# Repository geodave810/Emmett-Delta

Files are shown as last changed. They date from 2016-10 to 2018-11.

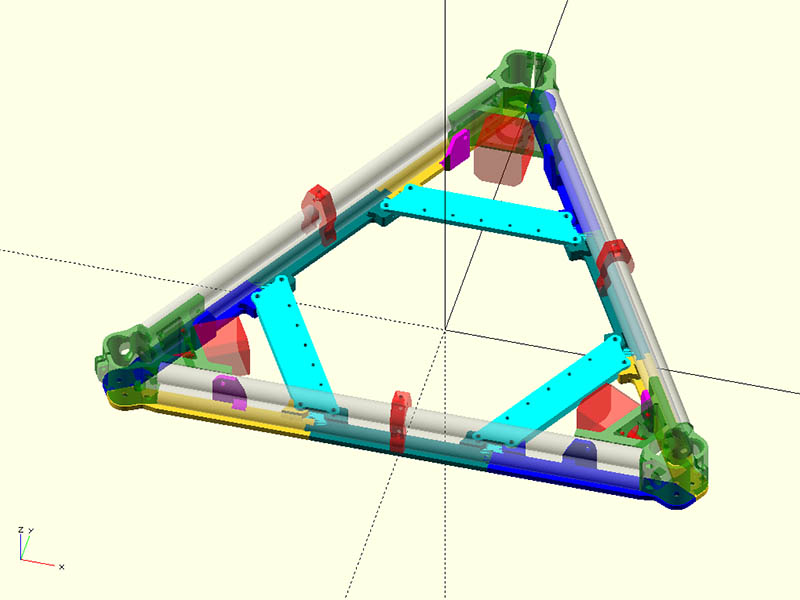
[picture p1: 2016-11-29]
EMT12_Horizontal_EMT12_Vertical/BottomFrame/BottomDoveTailFrame_300mmOD_Rev30.jpg

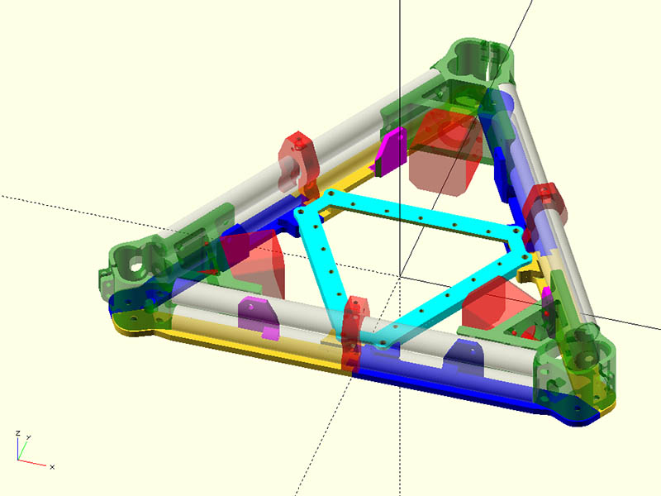
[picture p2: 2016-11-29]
EMT12_Horizontal_EMT12_Vertical/BottomFrame/BottomDoveTailFrame_210mmOD_Rev30.jpg

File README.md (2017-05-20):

# Emmett-Delta
Delta 3d Printer using Electrical Metal Tubing (EMT)

For details about this Delta 3d printer see the build log & discussion here:
<a href="http://www.openbuilds.com/builds/emmett-delta.3052/">Emmett-Delta</a>

I have added an animation file that shows how all the parts go together for Option 3 build
The animation was created using <a href="https://github.com/PRouzeau/OpenSCAD-Delta-Simulator">PRouzeau OpenSCA-Delta-Simulator</a>

10/31/2016 Update:
There are several different build options for this Delta & I am just getting
all these files together on Github.  Each Option will have its own file folder.
There is a BOM spreadsheet file, but it needs to be updated some.

Option 1:
3/4" EMT Horizontals and V-Slot 2060 extrusions for the Verticals.
(This is what I originally set out to build, but changed to the Option 3 build)

Option 2:
3/4" EMT Horizontals & 4x 1/2" EMT Verticals on each column.
You can also find his Cobalt Griffonary's nice build log of this configuration here:

https://cobaltgriffonary.blogspot.ca/2016/10/project-proteus-delta-part-1.html
https://cobaltgriffonary.blogspot.ca/2016/10/project-proteus-delta-part-2.html
https://cobaltgriffonary.blogspot.ca/2016/11/project-proteus-delta-part-3.html
https://cobaltgriffonary.blogspot.ca/2016/11/project-proteus-delta-part-4.html
https://cobaltgriffonary.blogspot.ca/2016/11/project-proteus-delta-part-5.html
https://cobaltgriffonary.blogspot.ca/2016/12/project-proteus-delta-part-6.html
https://cobaltgriffonary.blogspot.ca/2017/01/project-proteus-delta-part-7.html
https://cobaltgriffonary.blogspot.ca/2017/05/project-proteus-delta-part-8.html

Option 3:
1/2" EMT Horizontals & 4x 1/2" EMT Verticals on each column.
(This is the build I am doing & this has the most current changes)

Option 4:
1/2" PVC Horizontals & 4x 1/2" EMT Verticals on each column.

Option 5:
1/2" PVC Horizontals & 4x 1/2" PVC Verticals on each column.
(I have not uploaded the vertex files for this yet)

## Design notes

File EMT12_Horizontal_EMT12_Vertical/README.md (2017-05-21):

Update Info 5/21/2017

The build I am planning should have a build diameter of 200mm x 590mm height.  I am currently redoing the vertex parts for this version & printing them this week.

EMT Cut Lengths:
12x 700mm Lengths for Vertical 1/2" EMT
12x 266.5mm Lengths for Horizontal 1/2" EMT

This folder consists of the files specific to the 1/2"EMT Horizontal & 1/2" EMT Vertical Build.
The Filament Holder, HeatBed Brackets, P/S Brackets & various jigs can be found in folders under the main folder.

The reason they are not in this folder is because the openscad used to generate the STL files
has options for the various builds.

https://github.com/geodave810/Emmett-Delta/tree/master/FilamentHolder

https://github.com/geodave810/Emmett-Delta/tree/master/HB_Brackets

https://github.com/geodave810/Emmett-Delta/tree/master/PS_Brackets

https://github.com/geodave810/Emmett-Delta/tree/master/Jigs

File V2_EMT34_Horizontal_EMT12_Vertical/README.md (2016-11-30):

In an effort to make the vertex parts more consistant between the different configurations,
I am modifying the 3/4" EMT Horizontals.  This will use a quite a bit less plastic as well.
The Vertex_2x_EMT34H_4xEMT12V_V2_rev101.stl file can be used for bottom or top but has no belt adjustment
TheVertexTop_2x_EM34TH_4xEMT12V_V2_rev101.stl has Belt adjustment & also uses 2 pipes on each side.

The Heat Bed Brackets can be found in the folder:

https://github.com/geodave810/Emmett-Delta/tree/master/HB_Brackets

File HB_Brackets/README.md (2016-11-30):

These are the Heat Bed Brackets for the different options of Emmett-Delta Build.
There are 3 different STL files as well as an openscad file that uses the .dxf file for the profiles.

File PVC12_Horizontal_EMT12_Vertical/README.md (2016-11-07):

These are the files you need if configuring this build for 1/2" PVC for the Horizontals & 1/2" EMT for the Verticals.

The big advantage to this configuration is drill the mounting holes should be easier with PVC than with EMT.

For a 300mm Build plate, the horizontal PVC would only be 16.4" long & only 6.4" between Vertex screw hole &
where the build plate connects to Heat Bed Bracket.

See the HB_Bracket & PS_Brackets folder fot the bracket to hold the Heat Bed & Power Supply
https://github.com/geodave810/Emmett-Delta/tree/master/HB_Brackets

https://github.com/geodave810/Emmett-Delta/tree/master/PS_Brackets

See the following folder for parts that mount to the Vertical 1/2" EMT & Idler bracket

https://github.com/geodave810/Emmett-Delta/tree/master/EMT12_Horizontal_EMT12_Vertical

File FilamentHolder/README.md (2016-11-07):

This is what I am using for the Filament holder with this build.

The original design for this filament holder is here: http://www.thingiverse.com/thing:508896

Here are the references to the modifications I did to this design which include openscad sources.

Customizable Spool Holder Base
http://www.thingiverse.com/thing:1751711

Parametric openscad Remix of Universal stand-alone filament spool holder
http://www.thingiverse.com/thing:1715713

Remix of Filament Guide Tube to convert to openscad and make Parametric
http://www.thingiverse.com/thing:1710043

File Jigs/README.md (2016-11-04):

This folder is for assorted Jigs I am using with building this design.

The Horizontal Pipe Drill Jigs are to help drill straight holes thru center of the Pipes.
I would still recommend using a drill press to drill the holes.
There is a drill jig for 1/2" EMT, 3/4" EMT & 1/2" PVC pipe.

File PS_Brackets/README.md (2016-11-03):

These are brackets that allow you to mount a Power Supply to one side of the Delta on the bottom 2 pipes.
For the Extended Brackets, you will need to mirror 1 of them for the other side.  The extended brackets
should work better for smaller Build Diameter like 200mm.  See the animation file for how these look assembled.

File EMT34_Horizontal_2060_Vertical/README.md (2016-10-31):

These are the files for building a Emmett-Delta using 3/4" EMT for the Horizontals & V-Slot 2060 for the Verticals.

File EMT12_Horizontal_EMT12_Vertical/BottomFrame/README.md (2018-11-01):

This is a frame assembly that helps to pull all the parts together.
With this method, the horizontal 1/2" EMT should be able to stay in place
by connecting the vertex parts to this & using the vertex brackets.
This will save you from having to drill holes thru the horizontal 1/2" EMT.

The openscad source file references Vertex_2x_EM12TH_4xEMT12V_rev100.stl

Before printing any of these parts, I would recommend printing the file:
BottomDoveTailFrame_Test_Rev30.stl first.
This should give you a good indication of the fit of the dovetails & screw holes.

The holes are sized for M4 or #8 screws on the dovetail vertex mounting holes
The locknut traps are sized for #8 locknuts.  Change the variable:
M4Nut_OD = 9.4;   //If you want to use M4 screws & locknuts
The holes for mounting electronics brackets or electronics on the inside frame
are sized for M3 Screws.

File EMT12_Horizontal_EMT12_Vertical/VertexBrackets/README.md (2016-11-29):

This folder contains the brackets used to hole the 1/2" EMT horzontal pipe to the Vertex and/or Dovetail Inner Frame.

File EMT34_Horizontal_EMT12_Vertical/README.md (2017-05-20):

These are the Vertex and additionals Parts you need if you are building the Emmett-Delta with 3/4" EMT Horizontals & 1/2" EMT Verticals.

You can also find his Cobalt Griffonary's nice build log of this configuration here:
https://cobaltgriffonary.blogspot.ca/2016/10/project-proteus-delta-part-1.html
https://cobaltgriffonary.blogspot.ca/2016/10/project-proteus-delta-part-2.html
https://cobaltgriffonary.blogspot.ca/2016/11/project-proteus-delta-part-3.html
https://cobaltgriffonary.blogspot.ca/2016/11/project-proteus-delta-part-4.html
https://cobaltgriffonary.blogspot.ca/2016/11/project-proteus-delta-part-5.html
https://cobaltgriffonary.blogspot.ca/2016/12/project-proteus-delta-part-6.html
https://cobaltgriffonary.blogspot.ca/2017/01/project-proteus-delta-part-7.html
https://cobaltgriffonary.blogspot.ca/2017/05/project-proteus-delta-part-8.html

I have also included Cobalt Griffonary's basic BOM list in this for this configuration in this folder

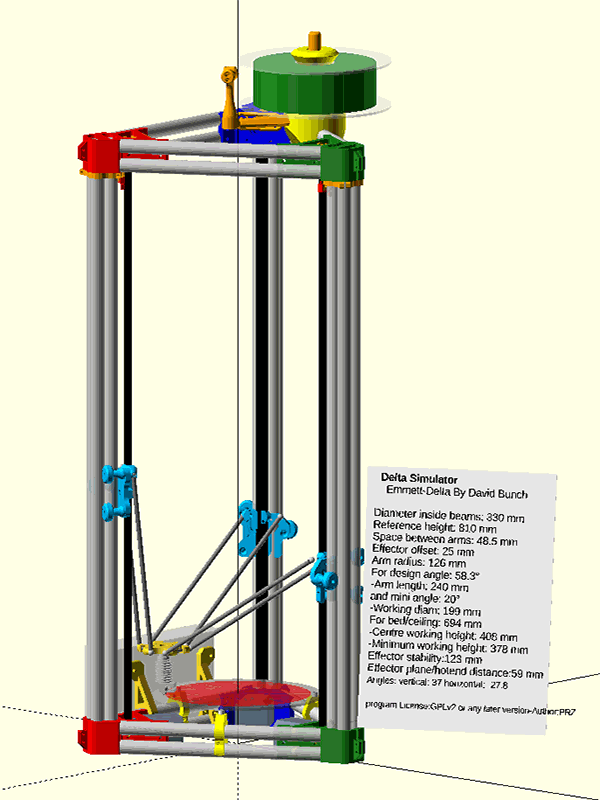
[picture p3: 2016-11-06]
Animations/Emmett_Animation_EMT12x266mmH_EMT12x800mmV.gif

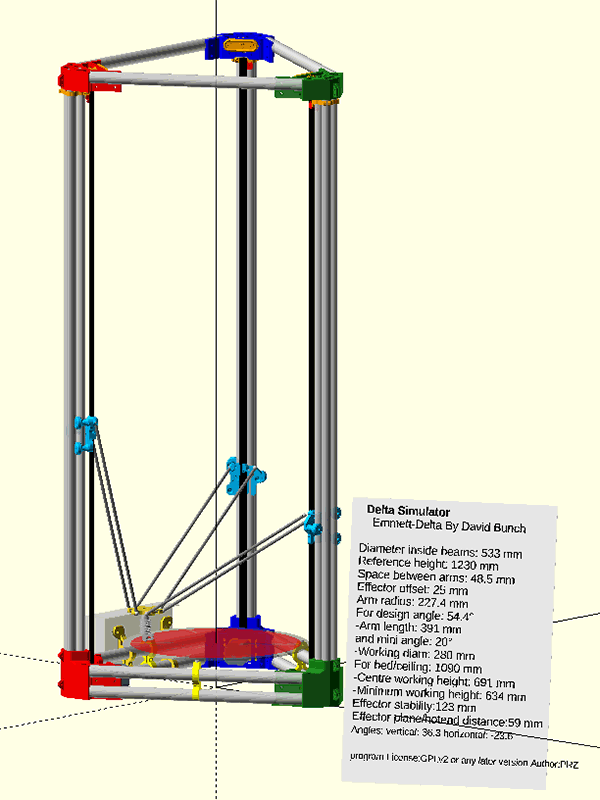
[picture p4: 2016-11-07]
Animations/Emmett_Delta_EMT34x420mmH_EMT12x1220mmV.gif

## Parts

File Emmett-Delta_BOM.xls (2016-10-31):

2016-01-08 | Bill of Materials for Emmett Delta Printer
Quantity | Description | Cost | Total Cost |  | Totals | Purchase Link
 | Plastic Filament |  |  |  |  | I am using Blue & Yellow PETG for the colors of plastic parts
3 | eSUN PETG Filament 1kg 1.75mm Plastic (My Hotend is 1.75mm) | $24.95 | $74.85 | $74.85 |  | http://www.intservo.com/products/esun-petg-filament-1-75mm-1kg-spool?variant=963058195
3 | eSUN PLA Filament 1kg 1.75mm Plastic (Option) | $21.99 | $65.97 |  | $74.85 | http://www.intservo.com/products/pla-filament-175?variant=800124003
 | Openbuilds Parts |  |  |  |  | I am using 1.75mm PETG filament, but you might need 3.00mm & prefer another type of Plastic
3 | 2060 Vertical Aluminum Extrusions (1000mm) | $15.50 | $46.50 |  |  | http://openbuildspartstore.com/v-slot-linear-rail/
 |  |  |  |  |  | My Delta is using 1000mm length, but you could probably go with 1500mm length
12 | Solid V Wheel Kit | $4.85 | $58.20 |  |  | http://openbuildspartstore.com/solid-v-wheel-kit/
 |  |  |  |  |  | You could also use The Delrin V Wheel or the Xtreme Solid V Wheels
6 | Eccentric Spacers 6mm for full size wheels | $2.00 | $12.00 |  |  | http://openbuildspartstore.com/eccentric-spacer/
2 | T-Nuts 1 pack of 25 | $4.95 | $9.90 |  |  | http://openbuildspartstore.com/tee-nuts-25-pack/
 |  |  |  |  |  | 12 T-Nuts for bottom Vertex, 6 or 12 T-Nuts on Top, 3 or 6 T-Nuts for Top Limit Switch Holder
3 | Smooth Idler Pulley Wheel Kit (For Idler pulley at top) | $5.45 | $16.35 |  |  | http://openbuildspartstore.com/smooth-idler-pulley-wheel-kit/
12 | M5 x 45mm for putting plates on both sides of wheels (Steel Option) | $0.20 |  |  |  | http://openbuildspartstore.com/low-profile-screws-m5/
3 | M5 x 40mm for idler pulley (Steel Option) | $0.20 |  |  |  | http://openbuildspartstore.com/low-profile-screws-m5/
12 | 6mm spacers for wheels on both sides | $0.20 | $2.40 |  |  | http://openbuildspartstore.com/aluminum-spacers/
9 | Precision Shim - 10x5x1mm (Think you can get about the same thing from MrMetric | $0.25 |  |  |  | http://openbuildspartstore.com/precision-shim-10x5x1mm/
 | Shipping $10 to $20 depending on where you are |  | $10.00 | $155.35 | $230.20
 | Local Electrical Conduit Purchase from Home Depot or Lowes (Check OD to be 23.5mm or .925")
2 | 2 - 3/4" x 10' EMT (Electrical Conduit from Home Depot or Lowes) | $3.63 | $7.26 | $7.26 | $237.46
1 | Pipe Cutter if you do not have one (This is one I like, but you can get a less expensive one) | $21.29 |  |  |  | http://www.homedepot.com/p/RIDGID-101-Tubing-Cutter-40617/100075014
 | MrMetric Parts
 | I am generally using 1 locknut per bolt, but added flatwashers to the list just in case
12 | M5x45 Stainless Button Head for Carriage Wheels (Option if you prefer Stainless like I do) | $0.18 | $2.16 |  |  | http://www.mrmetric.com/metric-fasteners/metric-button-socket-screw-ssa2/M11598.html
3 | M5x40 Stainless Button Head for idler Pulley (Option if you prefer Stainless like I do) | $0.23 | $0.69 |  |  | http://www.mrmetric.com/metric-fasteners/metric-button-socket-screw-ssa2/M11486.html
24 | M5X10 Button Head Socket Cap Screw (Only need 24 really for T-slot connect) | $0.10 | $2.40 |  |  | http://www.mrmetric.com/metric-fasteners/metric-button-socket-screw-ssa2/M11521.html
20 | M5x20 Button Head for Motor Mount Plate & Idler plate(18 needed) | $0.17 | $3.40 |  |  | http://www.mrmetric.com/metric-fasteners/metric-button-socket-screw-ssa2/M11526.html
9 | M5x16 Button Head (If Mounting Tetrahedron corners to top Vertex, 9 Tnuts needed also) | $0.13 | $1.17 |  |  | http://www.mrmetric.com/metric-fasteners/metric-button-socket-screw-ssa2/M11524.html
 | You could use Socket Cap instead, but only .01 cheaper & stick out further
100 | M5x.8 Nylon Insert Locknut Stainless Steel A2 (Price Break at 100) | $0.04 | $4.00 |  |  | http://www.mrmetric.com/metric-fasteners/ssa2-metric-nylock-nuts/M50352.html
100 | M5 Stainless Flat Washers (9.6 to 10mmOD, 5.3 to 5.48mmID) | $0.02 | $2.00 |  |  | http://www.mrmetric.com/Discount-Items/Metric-Washers/M60710.html
24 | M4x25mm Socket Cap Screw to attach Brackets around Pipe & vertex | $0.13 | $3.12 |  |  | http://www.mrmetric.com/metric-fasteners/metric-socket-head-cap-screws-ssa2/M10622.html
 | If you using extended brackets, you will need 1 more bolt & locknut per bracket
24 | M4x25mm Button Heads (These look better than Socket head, but a little bit more money $5.52 instead $3.12) | $0.23 | $5.52 |  |  | http://www.mrmetric.com/metric-fasteners/metric-button-socket-screw-ssa2/M11517.html
12 | M4x16mm Button Heads (2 on each vertex for Extended Bracket) | $0.08 | $0.96 |  |  | http://www.mrmetric.com/metric-fasteners/metric-button-socket-screw-ssa2/M11514.html
36 | M4x35mm Socket Head Stainless (If Drilling pipe instead of using brackets $3.60) | $0.15 |  |  |  | http://www.mrmetric.com/metric-fasteners/metric-socket-head-cap-screws-ssa2/M10727.html
 | or you can use 8-32x1 1/2" Phillips head screws & locknuts from local hardware instead of M4x35mm bolts
 | Button heads would look better, but cannot get this length in Button head
100 | M4 Locknuts (Get 100 to make sure you have enough) | $0.02 | $2.00 |  |  | http://www.mrmetric.com/metric-fasteners/ssa2-metric-nylock-nuts/M50351.html
12 | M3x10mm Socket Cap Screws (12 for mounting Motors to Motor Mount) | $0.05 | $0.60 |  |  | http://www.mrmetric.com/metric-fasteners/metric-socket-head-cap-screws-ssa2/M10605.html
3 | M3x16mm Socket Cap Screws (to tighten EMT Clamp that HeatBed attaches to, 14mm length will also work) | $0.06 | $0.18 |  |  | http://www.mrmetric.com/metric-fasteners/metric-socket-head-cap-screws-ssa2/M10608.html
6 | M3x20mm Socket Cap Screws (To tighten parts on EMT on Tetrahedron top if you are using this option) | $0.06 | $0.36 |  |  | http://www.mrmetric.com/metric-fasteners/metric-socket-head-cap-screws-ssa2/M10611.html
100 | M3 Locknuts | $0.03 | $3.00 |  |  | http://www.mrmetric.com/metric-fasteners/ssa2-metric-nylock-nuts/M50350.html
 | M3 Jam Nuts (In case you need these $0.03 if you order 100) | $0.05 |  |  |  | http://www.mrmetric.com/metric-fasteners/ssa2-metric-jam-nut-m3/
 | 14mm length will probably also work, but 16mm is more of standard size
 | I also need bolts to connect Traxxas Rods, but not sure what Length or Size yet
 | Shipping $6 & free shipping of $50 |  | $6.00 | $37.56 | $275.02
 | TriDPrinting Parts
3 | Nema 17 Stepper Motor (76oz-in torque) | $16.65 | $49.95 |  |  | http://www.tridprinting.com/Electronics/
8 | GT2 Belt (I probably only need 7 Meters, but want to make sure I have enough) | $2.50 | $20.00 |  |  | http://www.tridprinting.com/Mechanical-Parts/
1 | GT2 Belt Drive Gear 16 Tooth 16T, 2mm Pitch, 5mm bore (Per 3) | $6.95 | $6.95
1 | 400mm Assembled Traxxas Rods (Set of 6) | $44.95 | $0.00
 | You could save money by buying Unassembled version for $25.95 | $25.95 | $25.95
1 | Mean Well 12v or 24v P/S (I will probably use 12v) | $39.95 | $0.00
 | You can buy a less expensiver P/S on Amazon, but I do want to make sure P/S is Reliable | $25 | $25.00
 | Shipping |  | $21.95 | $149.80 | $424.82
 | Think3dprint3d
1 | Duet pcb 32bit 0.85 | $123.24 | $123.24 |  |  | https://www.think3dprint3d.com/Duet
 | DHL Shipping from UK |  | $23.08 | $146.32 | $571.14
 | SeeMeCNC (I may not use heat bed, if I decide to keep my delta at the larger size)
1 | ONYX Round PCB Heated Bed (rev7) 310OD, 280mm Heated | $69.00 | $69.00 |  |  | http://seemecnc.com/collections/parts-accessories/products/onyx-round-pcb-heated-bed?variant=377802937
 | 12 3mm diameter mounting holes spaced on a 300mm diameter pattern
1 | Rostock MAX Boro Glass Build Plate 310mm | $35.00 | $35.00 |  |  | http://seemecnc.com/collections/parts-accessories/products/boroscillicate-glass-build-plate-310mm
 | Not sure what shipping cost is here |  |  | $104.00 | $675.14
 | MatterHackers
1 | E3D-V6 HotEnd Full Kit - 1.75mm Universal (with Bowden add-on) | $83.00 | $83.00 | $83.00 | $758.14 | https://www.matterhackers.com/store/printer-accessories/v6-hotend-full-kit-1.75mm-universal-with-bowden
 | Might need a plate for this also from ultibots.com or another source | $6.95 |  |  |  | http://www.ultibots.com/mount-plate-6mm-groove/
 | Print These Parts (I am planning to print most parts at 50% infill using PETG Plastic) | Oz. weight |  |  | Print Time Each
 | Use EMT_Calculator_rev32.scad to calculate the size of your Emmmett Delta you want
3 | VertexTop_1xEMTAtTop_SideMount_2060V_WithEars_rev43_repaired.stl | 3.80 | 11.40 |  | 7:43:56 | 3.8oz each at 50% infill & print time of 7:43:56
 | VertexTop_1xEMTAtBot_SideMount_2060V_rev43_repaired.stl (option if you want EMT Level with bottom of Top Vertex)
3 | VertexBot_2xEMTSideMount_H_2060V_rev43_repaired.stl | 7.60 | 22.80 | 34.20 | 14:16:32 | 7.6oz each at 50% and Print Time of 14:16:32
3 | carriage_20x60_Rev20_repaired.stl
 | I may end up cutting an aluminum plate, to strengthen carriage & do away with backplate
3 | BackPlate_20x60_Rev20_repaired.stl (You might not need the backplate, but seemed better with it to me)
 | (If not using BlackPlate, you will only need M5x30mm for the carriage instead of the M5x45)
 | Effector of your choosing (I made redesign one later for my use)
1 | Delta_EMT_LimitSwitch_120deg_3x_rev2_repaired.stl (This is 3 of them in one file) | 0.43 | 0.43 |  | 1:02:35 | .43oz for 3x at 50% infill and Print time of 1:02:35
3 | Idler_2holeMount_44mmHoleSpacing_rev8_repaired.stl (Allows for some Belt tensioning) | 0.35 | 1.05 |  | 0:39:08
1 | EMT_IdlerTaper_3x_Shim_repaired.stl | 0.12 | 0.12 |  | 0:24:47 | .12oz for 3x at 50% infill and Print time of 0:24:47
3 | MotorMount_rev4_repaired.stl (Allows for some Belt tensioning) | 0.49 | 1.47 |  | 0:59:42 | .49oz for 1x at 50% infill and Print time of 0:59:42
 | You have 2 options with mounting the EMT to the Vertex parts, either drilling EMT or using brackets
 | It is probably easier to use the brackets, but it is more plastic to print
2 | EMT_SnglSquareDrillGuide_2Holes_Rev2_repaired.stl (Use this for drill guide if drilling EMT)
 | If not drilling, these are the brackets to print
12 | EMT_BotSideHoldingBracket_1x_rev6_repaired.stl (There is also a 2x & 4x of this part) | 0.37 | 4.44 |  | 0:32:46 | .37oz for 1x at 50% infill and Print time of 0:32:46
 | If it is too tight a space to get nut on the inside top, the folling part can be used
 | EMT_BotSideHoldingBracket_Extended_1x_rev5_repaired.stl (optional to use instead of the previous part) | 0.41 |  |  | 0:42:57 | .41oz for 1x at 50% infill and Print time of 0:42:57
12 | EMT_TopSideHoldingBracket_1x_rev5_repaired.stl | 0.29 | 3.48 |  | 0:28:58 | .29oz for 1x at 50% infill and Print time of 0:29:58
 | If it is too tight a space to get nut on the inside top, the folling part can be used
 | EMT_TopSideHoldingBracket_Extended_1x_rev5_repaired.stl | 0.32 |  |  | 0:35:28 | .32oz for 1x at 50% infill and Print time of 0:35:28
1 | EMT_TopBracketNamePlate_rev4_repaired.stl (Option of putting Name plate bracket instead of 2 top brackets)
1 | EMT_Name_Rev2_repaired.stl (If you want to Add the EMMETT name to your printer)
1 | EMT_NameBlank_Rev2_repaired.stl (Print this in lighter color than Name, for the Name to be more visible)
 | If you are Adding Tetrahedron to the top, you need these 2 parts
3 | TetraBot_EMT_TopOfVertex_rev11_repaired.stl (These fit on top Vertex parts)
1 | parametric_Tetrahedron34_EMT_Apex_Rev1.stl (This fits at top of Tetrahedron
1 | EMT_Emmett_NameBracket_rev3_repaired.stl (Attach Name Bracket to Tetrahedron)
 | Use TetrahedronPipeLengthCalcs_Rev3.scad to calculate lengths of Pipe you need
 | (This is also shown in EMT_Calculator_rev32.scad)
 | I have only designed what is needed for the Frame and a carriage that uses Traxxas Rods, but may end up designing something for magnetic arms
 | I have designed several types of connections for the EMT, but not sure which I will use
3 | EMT_GlassBracket_12mmHt_rev8_repaired.stl (This I will probably attach a build plate support or glass plate to) | 0.48 | 1.44 |  | 0:54:06 | .48oz for 1x at 50% infill and Print time of 0:54:06
 | EMT_ConnectTwo_60Degs_Rev3_repaired.stl (Connect 2 EMT's at 60 degree angle)
 | EMT_SnglSquareMountingBracket_Rev5_repaired.stl (A simple mount, but probably will not use as it might rotate)
 | Total Ouces for Parts |  | 46.63
 | EMT_ConnectTwo_60Degs_Rev3_repaired.stl (Connect 2 EMT's at 60 degree angle)
 | Here are a few items on thingiverse I designed to possibly use with this Delta
 | http://www.thingiverse.com/thing:1226855 |  |  |  |  | Parametric Build Plate Support for Delta Printer
 | http://www.thingiverse.com/thing:1186676 |  |  |  |  | Three Magnet Connector for Delta Printer Arms
 | http://www.thingiverse.com/thing:1161094 |  |  |  |  | Parametric Limit Switch Holder for V-Slot
 | http://www.thingiverse.com/thing:1150496 |  |  |  |  | Parametric Tapered Spacer

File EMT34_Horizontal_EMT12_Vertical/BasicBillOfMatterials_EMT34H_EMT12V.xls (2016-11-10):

Note that all prices are in CAD
Part: | Source: | Units: | Unit Cost: | Sub total: | Notes:
Nema 17 motors | https://www.electronicgeek.ca/products/nema-17-stepper-motor-42byghw609-56oz-in-40mm-1-7a-4-lead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 | 4 | $16.50 | $66.00
endstop switchs | https://www.electronicgeek.ca/products/endstop-mechanical-limit-switch-ramps-1-4-with-wire?variant=16718415299 | 3 | $2.50 | $7.50
GT2 belts | https://www.electronicgeek.ca/products/gt2-open-ended-timing-belt?variant=1950518979 | 8 | $2.50 | $20.00
20 tooth GT2 pulleys | https://www.electronicgeek.ca/products/gt2-timing-pulley-20t-for-6-mm-belt-20-teeth?variant=10535363395 | 3 | $3.50 | $10.50
GT2 Idler 20 tooth | https://www.electronicgeek.ca/products/2gt-20-teeth-synchronous-wheel-pulley-wheel-perlin-passive-idler-pulley-wheel-bore-5mm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 | 3 | $4.50 | $13.50
12 TRAXIS 5347 | https://www.electronicgeek.ca/products/12pcs-lot-reprap-delta-kossel-mini-5347-delta-ball-headed-buckle-ball-caps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 | 1 | $6.00 | $6.00
12V 400Watt Power Supply | https://spool3d.ca/power-supply-12v-350w/ | 1 | $42.00 | $42.00
Power switch and socket | https://www.electronicgeek.ca/products/c14-inlet-power-socket-connector-plug-switch-fuse-iec-320 | 1 | $5.00 | $5.00
Ramps 1.4 kit | https://www.electronicgeek.ca/products/mega-2560-r3-1pcs-ramps-1-4-controller-5pcs-a4988-stepper-driver-module-for-1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 | 1 | $35.00 | $35.00
30 cm Borosilicate Glass Printbed | http://www.ultibots.com/borosilicate-print-surface-300mm-round/ | 1 | $46.81 | $46.81 | This is optional, you can also use a sheet of 6mm acyrlic from your local supplier if avalible
E3D Lite6 hot-end | https://www.smw3d.com/e3d-lite6/ | 1 | $53.50 | $53.50 | Alternate is: https://spool3d.ca/genuine-e3d-lite6-bowden-hotend-kit-1-75mm-universal/
Solid v-wheels | http://openbuildspartstore.com/solid-v-wheel-kit/ | 9 | $6.52 | $58.68
3/4 inch electrical conduit | Local hardware store/building supply store | 2 | $9.29 | $18.58 | 1 unit = 10 feet
1/2 inch electrical contuit | Local hardware store/building supply store | 6 | $5.49 | $32.94 | 1 unit = 10 feet
3/8 inch steel rod stock | Local hardware store/building supply store | 3 | $1.29 | $3.87 | 1 unit = 3 foot length
M5x45mm socket head screw | Local hardware store/building supply store | 12 | $0.80 | $9.60
M5x20mm socket head screw | Local hardware store/building supply store | 18 | $0.90 | $16.20
M5 Lock nuts | Local hardware store/building supply store | 50 | $0.46 | $23.00
1/8 inch washers (35 pack) | Local hardware store/building supply store | 1 | $2.49 | $2.49 | Optional, only needed if you use a hand drill for the horizontals
8-32x 1.5 inch socket head screws | Local hardware store/building supply store | 36 | $0.99 | $35.64
8-32 nylocknuts | Local hardware store/building supply store | 36 | $0.29 | $10.44
m3x10mm pan head screws | Local hardware store/building supply store | 12 | $0.33 | $3.96
m3x20mm cap screws | Local hardware store/building supply store | 18 | $0.35 | $6.30 | Recommend buying lots of extra of these, there's always a use for them
m3 lock nuts | Local hardware store/building supply store | 15 | $0.25 | $3.75
M4x20mm pan head screws | Local hardware store/building supply store | 12 | $0.46 | $5.52
m2x10mm pan head screws | Local hardware store/building supply store | 6 | $0.26 | $1.56 | Used for mounting endstop switches
m2 nuts | Local hardware store/building supply store | 6 | $0.22 | $1.32
5-minute epoxy 14ml tube | Local hardware store/building supply store | 3 | $10.69 | $32.07
Total Cost: |  |  |  | $571.73

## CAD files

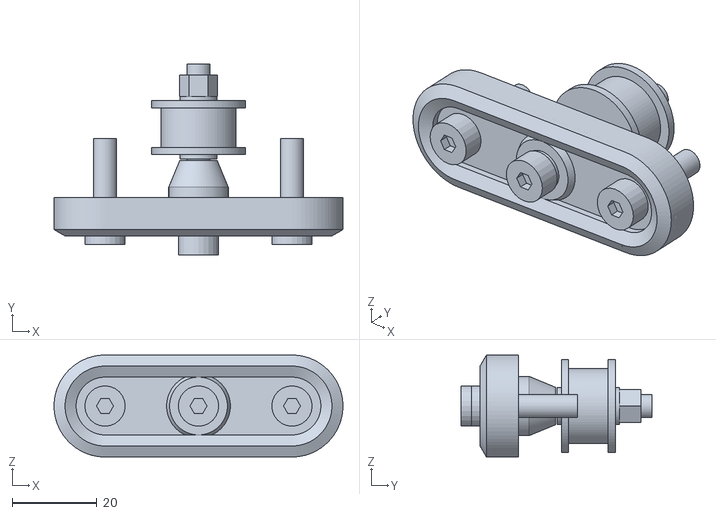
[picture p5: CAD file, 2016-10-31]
EMT34_Horizontal_2060_Vertical/Idler_2holeMount_44mmHoleSpacingAssembly_rev8.stl
68.0 x 45.0 x 24.0

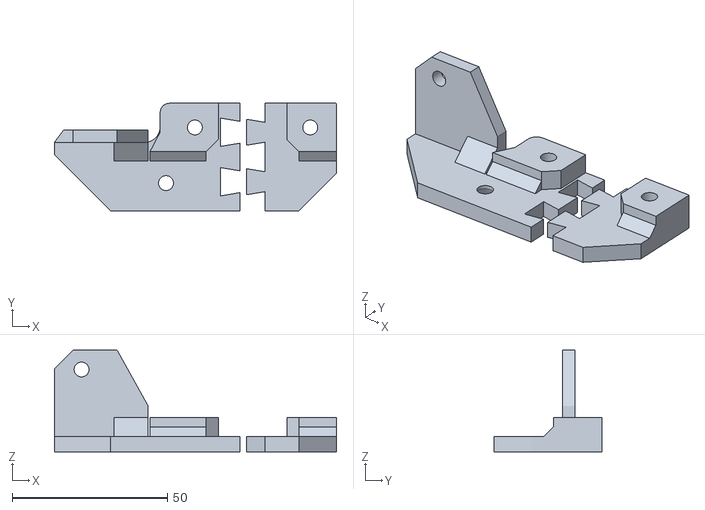
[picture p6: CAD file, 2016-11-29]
EMT12_Horizontal_EMT12_Vertical/BottomFrame/BottomDoveTailFrame_Test_Rev30.stl
90.7 x 34.6 x 32.8

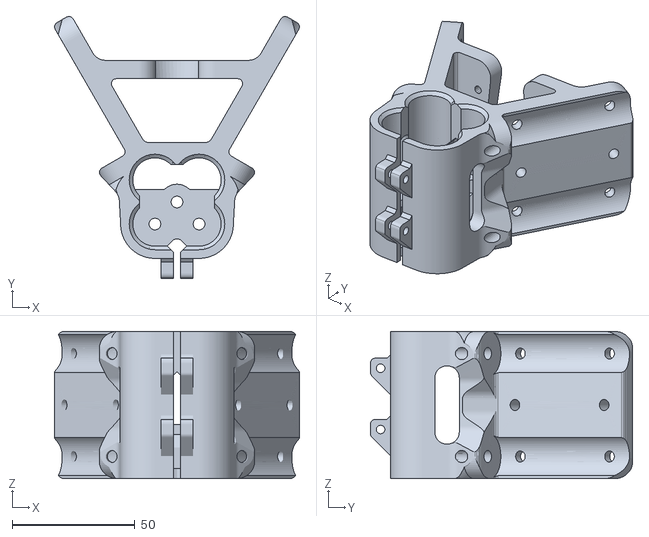
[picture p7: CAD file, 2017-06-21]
EMT12_Horizontal_EMT12_Vertical/VertexBottomTall_2x_EM12TH_4xEMT12V_rev117.stl
99.9 x 106.9 x 60.0

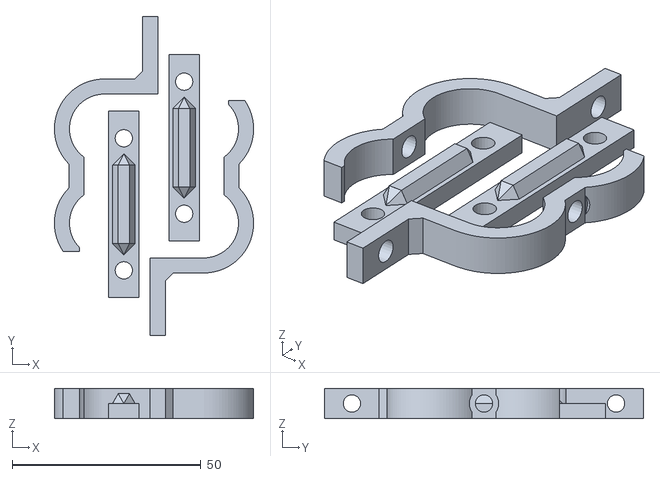
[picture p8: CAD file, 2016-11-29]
EMT12_Horizontal_EMT12_Vertical/VertexBrackets/EMT_18mmVertex_SimpleExtendedBrackets_Rev2.stl
52.8 x 84.5 x 8.00

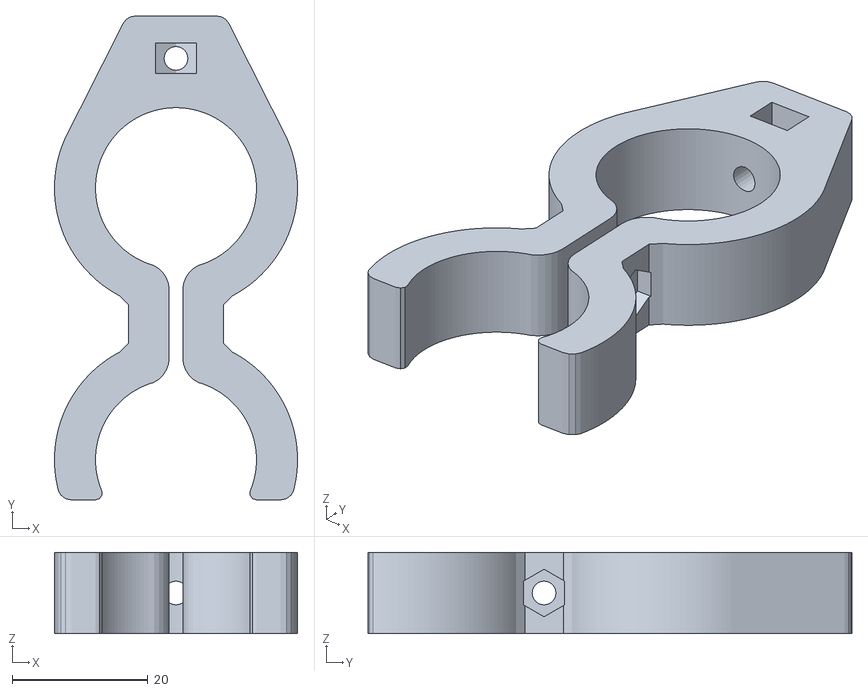
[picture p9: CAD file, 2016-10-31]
EMT34_Horizontal_2060_Vertical/EMT_GlassBracket_12mmHt_rev8.stl
35.8 x 71.3 x 12.0

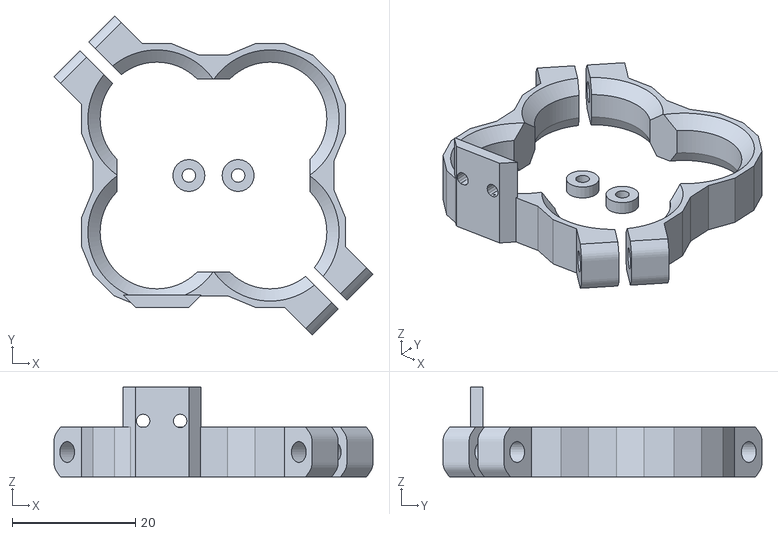
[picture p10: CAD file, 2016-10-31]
EMT34_Horizontal_EMT12_Vertical/Delta_EMT_MicroMech_LimitSwitch2PartBracket_Rev16.stl
51.8 x 51.8 x 14.6

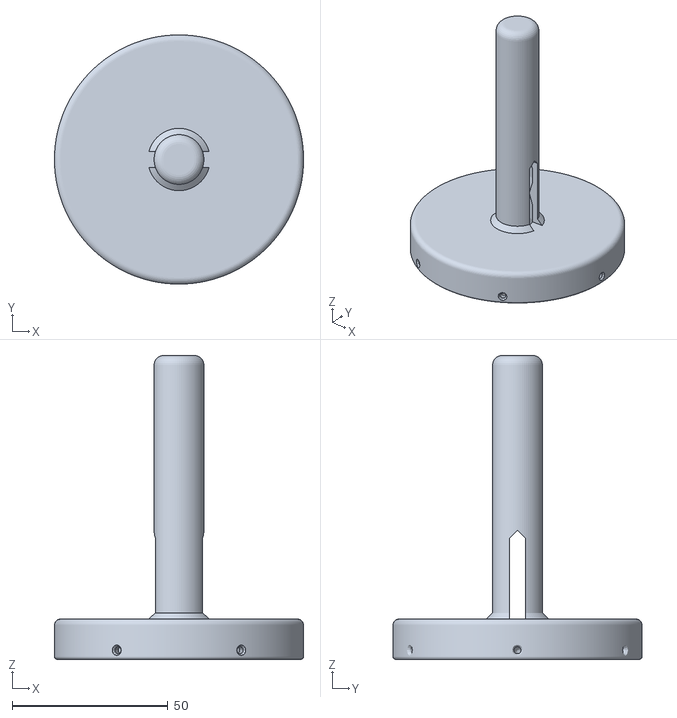
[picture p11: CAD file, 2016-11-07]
FilamentHolder/SpoolSpindle_Mod_Rev15.stl
80.0 x 80.0 x 97.6

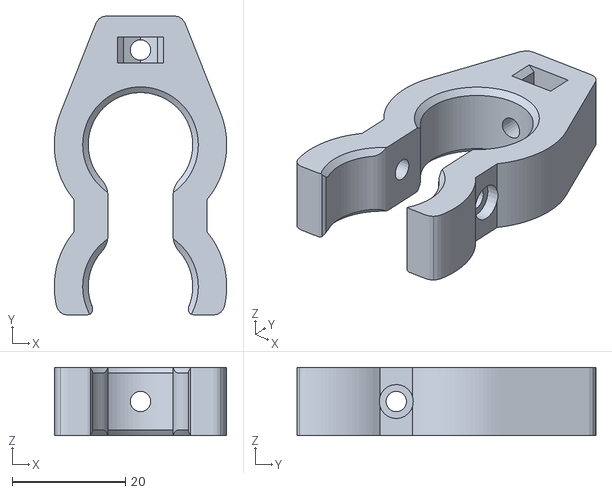
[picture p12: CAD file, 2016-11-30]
HB_Brackets/HB_EMT12_Bracket_rev3.stl
30.4 x 52.7 x 12.0

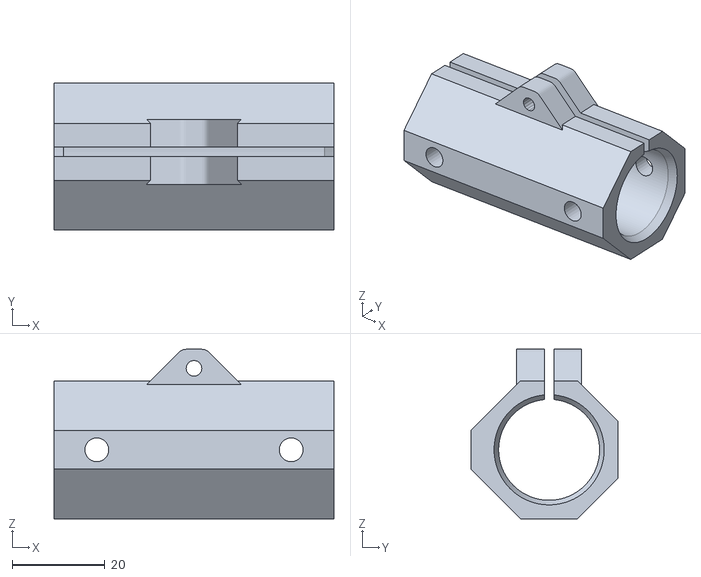
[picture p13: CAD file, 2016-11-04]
Jigs/HorizontalPipeDrill_Jig_12PVC_Rev3.stl
60.5 x 31.8 x 36.6

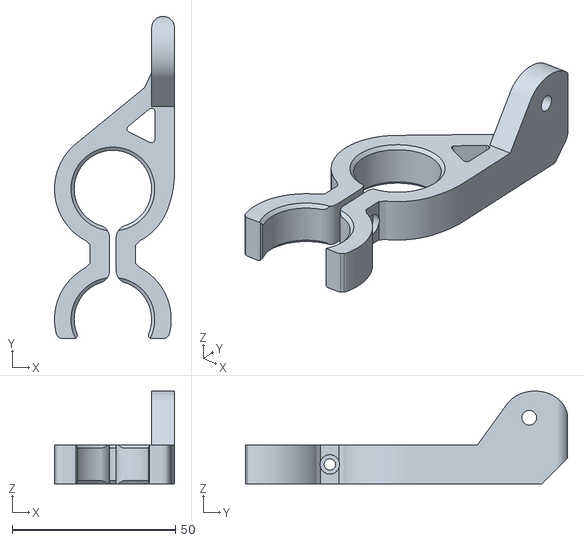
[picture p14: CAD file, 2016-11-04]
PS_Brackets/EMT34_PS_Bracket_Extend_Rev7.stl
36.8 x 98.9 x 28.5

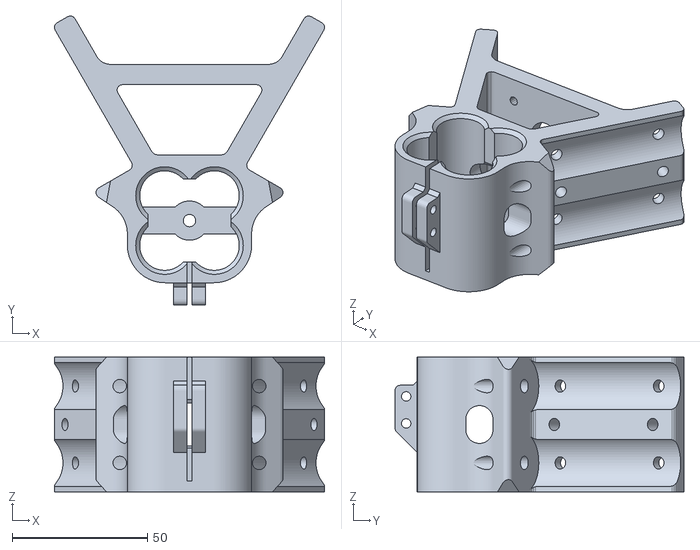
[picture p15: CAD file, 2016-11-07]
PVC12_Horizontal_EMT12_Vertical/Vertex_2x_PVC12H_4xEMT12V_rev93.stl
99.9 x 106.9 x 49.8

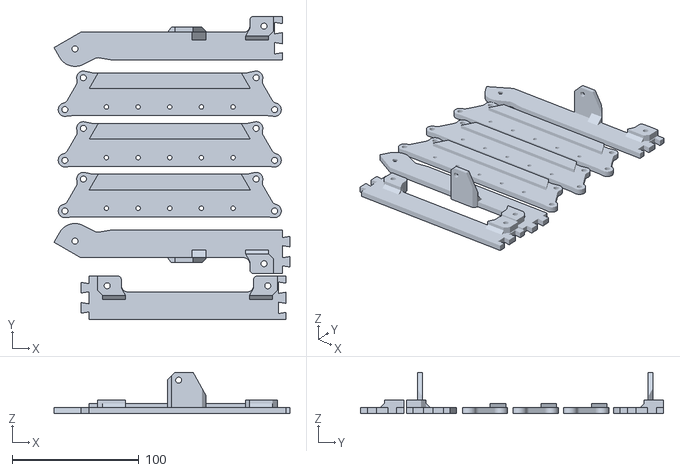
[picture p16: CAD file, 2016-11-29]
EMT12_Horizontal_EMT12_Vertical/BottomFrame/BottomDoveTailFrame_300mmOD_Parts_Rev30.stl
186.4 x 239.6 x 32.8

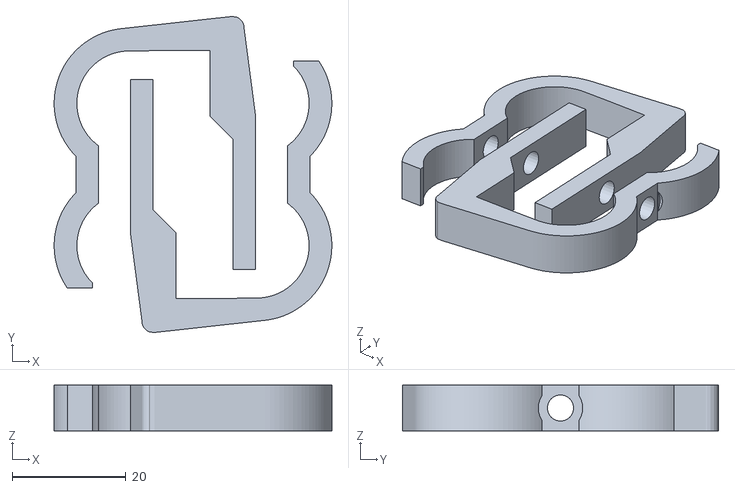
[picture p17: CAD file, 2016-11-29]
EMT12_Horizontal_EMT12_Vertical/VertexBrackets/EMT_18mmVertex_DoveTailBrackets_Rev2.stl
48.8 x 55.5 x 8.00

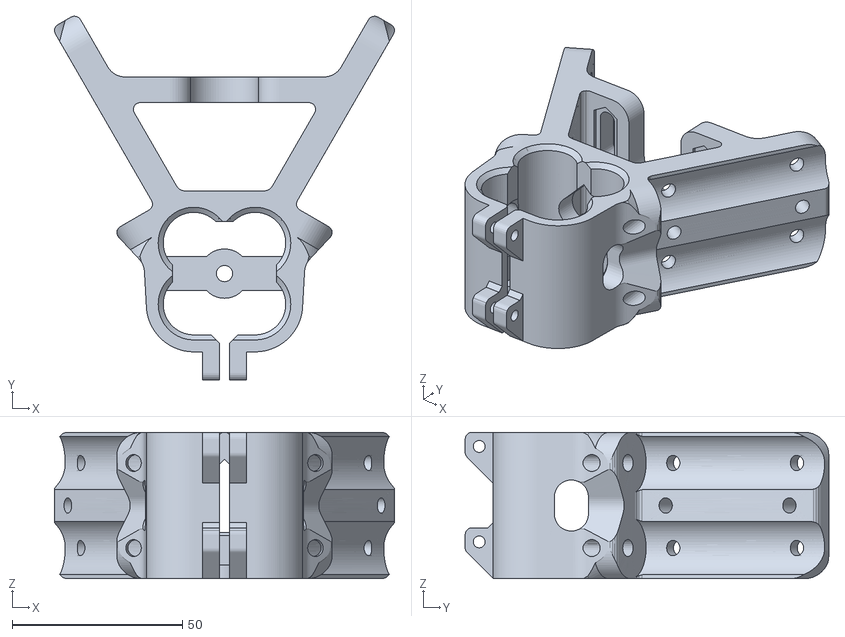
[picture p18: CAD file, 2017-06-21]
EMT12_Horizontal_EMT12_Vertical/VertexTop_2x_EM12TH_4xEMT12V_rev116.stl
99.9 x 106.9 x 43.0

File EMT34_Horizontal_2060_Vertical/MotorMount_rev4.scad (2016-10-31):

Len=44.4;
M3 = 3.4;
M5 = 5.5;
M16 = 16;
MotMove=0;
MotMHalf = MotMove / 2;
Ht=6;
$fn=24;
IresBig=108;
Y_Pt = 13.4;
X_Pt = 31.4;
module Plate()
{
    linear_extrude(height = Ht, center = false, convexity = 10)polygon(points = 
    [[-31.4,-13.4],[-35.27,-6.69],[-35.88,-7.07],[-36.44,-7.51],[-36.96,-8.01],
    [-37.44,-8.54],[-37.86,-9.12],[-38.23,-9.73],[-38.54,-10.38],[-38.78,-11.05],
    [-38.97,-11.74],[-39.09,-12.45],[-39.15,-13.16],[-39.13,-13.88],[-39.06,-14.59],
    [-38.91,-15.29],[-38.71,-15.98],[-38.44,-16.64],[-38.11,-17.28],[-37.72,-17.88],
    [-37.28,-18.44],[-36.79,-18.96],[-36.26,-19.44],[-35.68,-19.86],[-35.07,-20.23],
    [-34.42,-20.54],[-33.75,-20.79],[-33.06,-20.97],[-32.35,-21.09],[-31.64,-21.15],
    [-30.92,-21.14],[-30.21,-21.06],[-29.51,-20.92],[-28.82,-20.71],[-28.16,-20.44],
    [-27.52,-20.11],[-25.05,-18.69],[-24.58,-18.45],[-24.09,-18.29],[-23.58,-18.18],
    [-23.05,-18.15],[-22.4,-18.19],[-21.76,-18.32],[-21.14,-18.53],[-20.55,-18.82],
    [-20.01,-19.18],[-19.52,-19.61],[-19.15,-19.98],[-18.68,-20.39],[-18.14,-20.71],
    [-17.56,-20.95],[-16.95,-21.1],[-16.33,-21.15],[16.33,-21.15],[16.95,-21.1],
    [17.56,-20.95],[18.14,-20.71],[18.68,-20.39],[19.15,-19.98],[19.52,-19.61],
    [20.01,-19.18],[20.55,-18.82],[21.14,-18.53],[21.76,-18.32],[22.4,-18.19],
    [23.05,-18.15],[23.58,-18.18],[24.09,-18.29],[24.58,-18.45],[25.05,-18.69],
    [27.52,-20.11],[28.16,-20.44],[28.82,-20.71],[29.51,-20.92],[30.21,-21.06],
    [30.92,-21.14],[31.64,-21.15],[32.35,-21.09],[33.06,-20.97],[33.75,-20.79],
    [34.42,-20.54],[35.07,-20.23],[35.68,-19.86],[36.26,-19.44],[36.79,-18.96],
    [37.28,-18.44],[37.72,-17.88],[38.11,-17.28],[38.44,-16.64],[38.71,-15.98],
    [38.91,-15.29],[39.06,-14.59],[39.13,-13.88],[39.15,-13.16],[39.09,-12.45],
    [38.97,-11.74],[38.78,-11.05],[38.54,-10.38],[38.23,-9.73],[37.86,-9.12],
    [37.44,-8.54],[36.96,-8.01],[36.44,-7.51],[35.88,-7.07],[35.27,-6.69],
    [34.7,-6.33],[34.17,-5.91],[33.67,-5.46],[33.21,-4.96],[32.8,-4.42],
    [32.44,-3.85],[32.12,-3.25],[31.87,-2.63],[31.66,-1.98],[31.52,-1.32],
    [31.43,-0.65],[31.4,0],[31.43,0.65],[31.52,1.32],[31.66,1.98],
    [31.87,2.63],[32.12,3.25],[32.44,3.85],[32.8,4.42],[33.21,4.96],
    [33.67,5.46],[34.17,5.91],[34.7,6.33],[35.27,6.69],[35.88,7.07],
    [36.44,7.51],[36.96,8.01],[37.44,8.54],[37.86,9.12],[38.23,9.73],
    [38.54,10.38],[38.78,11.05],[38.97,11.74],[39.09,12.45],[39.15,13.16],
    [39.13,13.88],[39.06,14.59],[38.91,15.29],[38.71,15.98],[38.44,16.64],
    [38.11,17.28],[37.72,17.88],[37.28,18.44],[36.79,18.96],[36.26,19.44],
    [35.68,19.86],[35.07,20.23],[34.42,20.54],[33.75,20.79],[33.06,20.97],
    [32.35,21.09],[31.64,21.15],[30.92,21.14],[30.21,21.06],[29.51,20.92],
    [28.82,20.71],[28.16,20.44],[27.52,20.11],[25.05,18.69],[24.58,18.45],
    [24.09,18.29],[23.58,18.18],[23.05,18.15],[22.4,18.19],[21.76,18.32],
    [21.14,18.53],[20.55,18.82],[20.01,19.18],[19.52,19.61],[19.15,19.98],
    [18.68,20.39],[18.14,20.71],[17.56,20.95],[16.95,21.1],[16.33,21.15],
    [-16.33,21.15],[-16.95,21.1],[-17.56,20.95],[-18.14,20.71],[-18.68,20.39],
    [-19.15,19.98],[-19.52,19.61],[-20.01,19.18],[-20.55,18.82],[-21.14,18.53],
    [-21.76,18.32],[-22.4,18.19],[-23.05,18.15],[-23.58,18.18],[-24.09,18.29],
    [-24.58,18.45],[-25.05,18.69],[-27.52,20.11],[-28.16,20.44],[-28.82,20.71],
    [-29.51,20.92],[-30.21,21.06],[-30.92,21.14],[-31.64,21.15],[-32.35,21.09],
    [-33.06,20.97],[-33.75,20.79],[-34.42,20.54],[-35.07,20.23],[-35.68,19.86],
    [-36.26,19.44],[-36.79,18.96],[-37.28,18.44],[-37.72,17.88],[-38.11,17.28],
    [-38.44,16.64],[-38.71,15.98],[-38.91,15.29],[-39.06,14.59],[-39.13,13.88],
    [-39.15,13.16],[-39.09,12.45],[-38.97,11.74],[-38.78,11.05],[-38.54,10.38],
    [-38.23,9.73],[-37.86,9.12],[-37.44,8.54],[-36.96,8.01],[-36.44,7.51],
    [-35.88,7.07],[-35.27,6.69],[-34.7,6.33],[-34.17,5.91],[-33.67,5.46],
    [-33.21,4.96],[-32.8,4.42],[-32.44,3.85],[-32.12,3.25],[-31.87,2.63],
    [-31.66,1.98],[-31.52,1.32],[-31.43,0.65],[-31.4,0],[-31.43,-0.65],
    [-31.52,-1.32],[-31.66,-1.98],[-31.87,-2.63],[-32.12,-3.25],[-32.44,-3.85],
    [-32.8,-4.42],[-33.21,-4.96],[-33.67,-5.46],[-34.17,-5.91],[-34.7,-6.33],
    [-35.27,-6.69]]);

}

module M3Mount()
{
    union()
    {
        translate([0,0,-1])
        cylinder(d=M3,h=Ht+2);
        translate([-(M3/2),0,-1])
        cube([M3,MotMove,Ht+2]);
        translate([0,MotMove,-1])
        cylinder(d=M3,h=Ht+2);
    }
}
module MotorMount()
{
    union()
    {
        translate([0,-MotMHalf,-1])
        cylinder(d=M16,h=Ht+2,$fn=IresBig);
        translate([-(M16/2),-MotMHalf,-1])
        cube([M16,MotMove,Ht+2]);
        translate([0,MotMHalf,-1])
        cylinder(d=M16,h=Ht+2,$fn=IresBig);
    }
}
module MotorCone()
{
    translate([0,0,Ht-1.8])
    hull()
    {
        translate([0,-MotMHalf,0])
        cylinder(d1=22.3,d2=24.09,h=1.82,$fn=IresBig);
        translate([0,MotMHalf,0])
        cylinder(d1=22.3,d2=24.09,h=1.82,$fn=IresBig);
    }
}
module PunchHoles()
{
    MotorCone();
    MotorMount();
    translate([-15.5,-15.5,0])
    M3Mount();
    translate([15.5,-15.5,0])
    M3Mount();
    translate([-15.5,15.5,0])
    M3Mount();
    translate([15.5,15.5,0])
    M3Mount();
//    translate([-15.5,15.5,0])
//    cylinder(d=2.5,h=20);
// Mounting Plate Holes
    translate([-X_Pt,-Y_Pt,-1])
    cylinder(d=M5,h=Ht+2);
    translate([X_Pt,-Y_Pt,-1])
    cylinder(d=M5,h=Ht+2);
    translate([-X_Pt,Y_Pt,-1])
    cylinder(d=M5,h=Ht+2);
    translate([X_Pt,Y_Pt,-1])
    cylinder(d=M5,h=Ht+2);
}
difference()
{
    Plate();
    PunchHoles();
}

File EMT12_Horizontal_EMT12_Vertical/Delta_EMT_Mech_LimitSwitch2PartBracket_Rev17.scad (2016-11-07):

//Mechanical Limit Switch Bracket
//10/21/2016    By: David Bunch
//This is for a 20 x 10.5 x 6.5mm Mechanical Limit Switch
//With 2mm Hole Spacing 6.15mm apart
//I used 2 - M3x20mm screws with Locknuts for the Bracket
//and 2 - M2.5x12mm screws to mount the switch to the bracket

Ht = 16.1-4-4;          //Height of Limit Switch Bracket
EMT_OD=18.4;
M3 = 3.4;               //Holding Bolt Diameter hole
M2 = 2.8;               //Diameter of Limit Switch holes,

Spacer_On = 1;          //1 = Draw 2 spacers, 0 = No Spacers
Spacer_ID = 2.2;        //Interal Diameter of Screw hole for Spacer
Spacer_OD = 5.2;        //Outside Diameter of Spacer
Spacer_Ht = 2;          //Spacer height

Ht_2 = Ht / 2;
EMT_Rad = EMT_OD / 2;

EMT_Res = (round(((EMT_OD * 3.14)/4)/.7)*4);
echo(EMT_Res = EMT_Res);
EMT12_OD = 17.9;    //This is what I measured the 1/2" EMT pipes I am using to be
EMT12_Rad = EMT12_OD / 2;
M3_Res = 16;
echo(Ht = Ht);
EMT12OD_Res = (round(((EMT12_OD * 3.14)/4)/.7)*4);
$fn=24;

module LimitSwitch()
{
    translate([20-3,-(EMT_OD)-3-2,-11])
    rotate([-90,0,0])
    rotate([0,0,180])
    translate([0,0,-6.5])
    difference()
    {
        union()
        {
            color("blue",.5)
            cube([20,10.5,6.5]);
            translate([1.5,10.4,2])
            {
                color("silver",.5)
                {
                    cube([.5,4,3]);
                    translate([8,0,0])
                    cube([.5,4,3]);
                    translate([16.8,0,0])
                    cube([.5,4,3]);
                }
            }
            rotate([0,0,-5])
            translate([3,0,1])
            {
                cube([19,.5,4]);
                translate([19-2.25,-4.25,0])
                {
                    color("red",.5)
                    {
                        cylinder(d=4.5,h=4);
                        translate([-2.25,0,0])
                        cube([4.5,2.25+2,4]);
                    }
                }
            }
        }
        translate([5.3,7.7,-1])
        cylinder(d=2.5,h=8.5);
        translate([15,7.7,-1])
        cylinder(d=2.5,h=6.5+2);
    }
}
module Plate()
{
    mirror([1,0,0])
    linear_extrude(height = Ht, center = false, convexity = 10)polygon(points = 

    [[12.88,22.78],[11.5,21.4],[6.77,21.4],[2.29,19.54],[-2.29,19.54],
    [-6.77,21.4],[-11.63,21.4],[-16.11,19.54],[-19.54,16.11],[-21.4,11.63],
    [-21.4,6.77],[-19.54,2.29],[-19.54,-2.29],[-21.4,-6.77],[-21.4,-11.5],
    [-22.78,-12.88],[-12.88,-22.78],[-11.5,-21.4],[-6.77,-21.4],[-2.29,-19.54],
    [2.29,-19.54],[6.77,-21.4],[11.63,-21.4],[16.11,-19.54],[19.54,-16.11],
    [21.4,-11.63],[21.4,-6.77],[19.54,-2.29],[19.54,2.29],[21.4,6.77],
    [21.4,11.5],[22.78,12.88]]);
}
module EMT_Nut()
{
    translate([-1,21.4,Ht_2])
    rotate([-90,0,0])
    rotate([0,-90,0])
    difference()
    {
        linear_extrude(height = 6, center = false, convexity = 10)polygon(points = 
        [[8.23,-1.74],[8.23,1.74],[8.19,2.13],[8.08,2.51],[7.89,2.86],
        [7.64,3.16],[0,10.8],[-0.86,10.8],[-0.86,-10.8],[0,-10.8],
        [7.64,-3.16],[7.89,-2.86],[8.08,-2.51],[8.19,-2.13]]);
    }
}
module EMT_NutsSide()
{
    EMT_Nut();
    translate([8,0,0])
    EMT_Nut();
}
module PipeSlot()
{
    translate([-1,-1,-1])
    cube([2,EMT_OD*3,Ht+20]);
}
module Pipes4xCuts(EMT_Ht = Ht)
{
    for (x =[-1,1])
    {
        for (y = [-1,1])
        {
            translate([x*EMT_Rad,y*EMT_Rad,-1])
            cylinder(d=EMT_OD,h=EMT_Ht + 2,$fn=EMT_Res);
            translate([x*EMT_Rad,y*EMT_Rad,-.01])
//Chamfer bottom opening
            cylinder(d1=EMT_OD+4,d2=EMT_OD,h=2.01,$fn=EMT_Res);
            translate([x*EMT_Rad,y*EMT_Rad,EMT_Ht-2])
//Chamfer Top Pipe opening
            cylinder(d1=EMT_OD,d2=EMT_OD+2,h=2.01,$fn=EMT_Res);
        }
    }
}
module Pipes4x(EMT_Ht = Ht)
{
    for (x =[-1,1])
    {
        for (y = [-1,1])
        {
            difference()
            {
                translate([x*EMT_Rad,y*EMT_Rad,-1])
                cylinder(d=EMT_OD,h=EMT_Ht + 2,$fn=EMT_Res);
                translate([x*EMT_Rad,y*EMT_Rad,-2])
                cylinder(d=EMT_OD-2.8,h=EMT_Ht + 4,$fn=EMT_Res);
            }
        }
    }
}

module ExtendBracket()
{
    EB_Thk = 4;
    EB_HT = 8.5;
    difference()
    {
    translate([-2,-(19.4+EB_Thk),-EB_HT])
        cube([18,EB_Thk,EB_HT+Ht]);
        translate([-3,0,-1])
        {
            translate([5,-22,-2.3])
            rotate([-90,0,0])
            cylinder(d=M2,h=10,$fn=M3_Res,center=true);
            translate([14.7,-22,-2.3])
            rotate([-90,0,0])
            cylinder(d=M2,h=10,$fn=M3_Res,center=true);
        }
        translate([-2,-19.4-EB_Thk,-EB_HT-1])
        cylinder(d=3,h=EB_HT+2+Ht,$fn=4);
        translate([18-2,-19.4-EB_Thk,-EB_HT-1])
        cylinder(d=3,h=EB_HT+2+Ht,$fn=4);
        translate([-25,-21.4,-9.5])
        cube([50,10,9.5]);
    }
}
module Spacer()
{
    difference()
    {
        cylinder(d=Spacer_OD,h=Spacer_Ht);
        translate([0,0,-1])
        cylinder(d=Spacer_ID,h=Spacer_Ht+2,$fn=24);
    } 
}
module DrawFinal()
{
//    translate([0,0,Ht])
//    rotate([0,180,0])
    difference()
    {
        union()
        {
            rotate([0,0,90])
            difference()
            {
                union()
                {
                    Plate();
                    translate([0,0,0])
                    rotate([0,0,45])
                    {
                    EMT_NutsSide();
                    mirror([0,1,0])
                    EMT_NutsSide();
                    }
                }
                Pipes4xCuts();
                translate([0,0,-1])
                rotate([0,0,22.5])
                cylinder(d=34,h=Ht+2,$fn=8);
                rotate([0,0,45])
                {
                    PipeSlot();
                    mirror([0,1,0])
                    PipeSlot();
                }
                translate([0,0,Ht])
                cylinder(d=200,h=10);
                translate([0,0,-10])
                cylinder(d=200,h=10);
            }
            ExtendBracket();
        }
        rotate([0,0,45])
        {
            translate([26.6,0,Ht/2])
            rotate([90,0,0])
            cylinder(d=M3,h=16,$fn=24,center=true);
            translate([-26.6,0,Ht/2])
            rotate([90,0,0])
            cylinder(d=M3,h=16,$fn=24,center=true);
        }
    }
}
translate([0,0,Ht])
rotate([0,180,0])
{
    DrawFinal();
    %LimitSwitch();
}
if (Spacer_On == 1)
{
    translate([-4,0,0])
    Spacer();
    translate([4,0,0])
    Spacer();
}

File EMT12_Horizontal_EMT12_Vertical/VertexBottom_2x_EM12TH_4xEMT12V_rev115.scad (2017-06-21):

// Emmett-Delta 3D Printer 
// Based on Delta-Six Vertex Created by Sage Merrill
// Base on https://github.com/Jaydmdigital/Kossel_2020
// Released on Openbuilds.com
// which was Based on orginal design by Johann C. Rocholl (Kossel Printer)
// License = Attribution Share Alike - CC BY SA

//Modified by David Bunch to handle 3/4" Electrical Conduit Pipe for Horizontals

//Modified 2/1/2016 to handle 4x 1/2" Electrical Conduit Pipes Vertically 

//Modified 10/28/2016 to use 1/2"EMT both horizontal & Vertical
//Modified 5/23/2017 to make some minor adjustments

//06:26:45 print time at 50% infill PLA 2.89oz
//$vpt=[-4.8,-22,25.6];
//$vpr =[55,0,71.2];
//$vpd =435;
height = 43;
ExtendHt = 0;                       //Extend height above main part

EMT12_Hor_OD = 18.0;                  //For Visual display of acutal size of pipe
EMT12_Hor_Rad = EMT12_Hor_OD / 2;   //Calculate Pipe offset using actual pipe size

//Nomimal 1/2" EMT from HomeDepot site is .706" OD or 17.9324mm
//Nomimal 1/2" EMT from HomeDepot site is .622" ID or 15.7988mm
//Wall thickness .042" or 1.0668mm

EMT_OD = 18.0;                      //Originally used 18.4, but seemed too loose
                                    //after upgrading the extruder on my printer
                                    //Based on what worked for 3/4" on MPCNC
                                    //Adding .2mm to OD should be a good number
EMT12_OD = 18.0;
EMT12_Rad = EMT12_OD / 2;
EMT_Rad = EMT_OD / 2;
EMT_EndHole_OD = 8;
EMT_EndHole_Res = 36;

EMT_Hor_X = 24.32;          //Other version was 44.1432
EMT_Hor_Y = 17.46;          //Other Versionwas 18.7292
Ht_Half = height / 2;

Ht = 8;
M5 = 5.5;
M5Nut = 10.0;               //Locknut measures 9.1mm but adding 10%
                            //Used for Idler Mount bracket
                            //This should make it a little easier to put the Locknut on
Slot_Gap = 3;               //Gap width for tightening vertex against 4x EMT12
                            //increased from 2mm to 3mm to give more tightening
                            //in case pipes are too loose from print
Slot_Gap2 = Slot_Gap / 2;

M4 = 4.8;
M8 = 8.5;
M3 = 3.5;
M3_Res = 16;
M5_Res = 24;
PipeScrewDia = 4.5;   //Dia. of holes for Screws that mount EMT Pipe to Vertex
                       //Use 5.15 to 5.5 for M5, or 4.15 to 4.5 for M4
//EMT Horizontal Mounting Holes have 42mm spacing
Screw_X1_Offset = 43.63;
Screw_Y1_Offset = 16.99;
Screw_X2_Offset = 64.63;
Screw_Y2_Offset = 53.36;
Pipe_Qty = 2;

Pipe_Spacing = 25;      //Use +20 for pipe at bottom & -20 for pipe even with top

BaseThk = 4;
$fn=48;
PipeBaseThk=0;
IdlerMnt_X_Offset = 19;             //Idler Mount Bolt offset from center
                                    //Need at least 19mm for 4mm thick from motor outer cut
Idler_Move = 0;                     //I would use 6mm to 7mm max, but I am using 0
                                    //As I am going to take care of belt tensioning on the carriage
Pipe_Z = EMT12_Hor_Rad;
UpHt = 6;
Bot_EMT_Holes_ON = 1;               //Add surface & holes under outside 2 vertical EMT's, 1 = Yes
                                    //This is useful for more clearance to screw wooden base to vertex
TotHt = PipeBaseThk + height + ExtendHt;
echo("TotHt = ", TotHt);
echo("Ht_Half + PipeBaseThk = ",Ht_Half + PipeBaseThk);
echo(Pipe_Z = Pipe_Z);
//Makes each segment about .7mm and even number of segments
EMT12OD_Res = (round(((EMT12_OD * 3.14)/4)/.7)*4);       //Resolution of Chamfers
echo("EMT12OD_Res = ",EMT12OD_Res);

module EMT12_4xCut()
{
    for (x = [-1,1])
    {
        for (y = [-1,1])
        {
            translate([x * EMT12_Rad,y * EMT12_Rad,0])
            EMT12_1xPipe();
        }
    }
    translate([-30.7/2,-30.7/2,0])
    cube([30.7,30.7,height+2]);
    translate([-EMT12_Rad,-EMT_OD,0])
    cube([EMT_OD,EMT_OD,height+2]);
}
module EMT12_4xChamfer()
{
    Chamf_Ht = 1.5;
    CH_OD = EMT12_OD + Chamf_Ht + Chamf_Ht;
    mirror([0,0,1])
    {
        for (x = [-1,1])
        {
            translate([x * EMT12_Rad,EMT12_Rad,0])
            cylinder(d1=CH_OD,d2=EMT12_OD,h=Chamf_Ht + .01,$fn=EMT12OD_Res);
        }
//Changed the outer chamfer to hull after slicing inside flush at the back inside
        hull()
        {
                translate([-EMT12_Rad,-EMT12_Rad,0])
                cylinder(d1=CH_OD,d2=EMT12_OD,h=Chamf_Ht + .01,$fn=EMT12OD_Res);
                translate([EMT12_Rad,-EMT12_Rad,0])
                cylinder(d1=CH_OD,d2=EMT12_OD,h=Chamf_Ht + .01,$fn=EMT12OD_Res);
        }
    }
}
//Used for Vertical Pipes
module EMT12_1xPipe(E_Ht = height+2)
{
    cylinder(d=EMT12_OD,h=E_Ht,$fn=EMT12OD_Res);
}
module EMT12_1xPipeDisplay(E_Ht = height+2)
{
    difference()
    {
        cylinder(d=EMT12_OD,h=E_Ht,$fn=EMT12OD_Res);
        translate([0,0,-1])
        cylinder(d=EMT12_OD-2.8,h=E_Ht+2,$fn=EMT12OD_Res);
    }
}
module EMT12_Pipes()
{
    translate([0,0,BaseThk])
    rotate([0,0,0])
    {
        for (x = [-1,1])
        {
            for (y = [-1,1])
            {
                translate([x * EMT12_Rad,y * EMT12_Rad,0])
                EMT12_1xPipeDisplay(100);
            }
        }
    }
}
module Vertex_Outline()
{
    linear_extrude(height = height, center = false, convexity = 10)polygon(points = 
    [[42.35,74.7],[42.87,75.29],[43.57,75.63],[44.35,75.68],[45.09,75.43],
    [48.98,73.18],[49.57,72.67],[49.91,71.97],[49.97,71.19],[49.71,70.45],
    [21.42,21.44],[21.17,20.7],[21.22,19.92],[21.56,19.22],[22.15,18.71],
    [30.65,13.8],[31.19,13.34],[31.54,12.71],[31.65,12.01],[31.5,11.31],
    [31.11,10.71],[25.13,4.3],[24.69,3.77],[24.31,3.19],[24,2.56],
    [23.77,1.91],[23.61,1.23],[23.53,0.54],[23,-9],[22.94,-10.25],
    [22.88,-10.87],[22.78,-11.48],[22.65,-12.09],[22.5,-12.7],[22.33,-13.29],
    [22.12,-13.88],[21.8,-14.68],[21.53,-15.24],[21.22,-15.84],[20.87,-16.42],
    [20.5,-16.98],[20.1,-17.53],[19.68,-18.05],[19.23,-18.56],[18.76,-19.04],
    [18.26,-19.5],[17.75,-19.93],[17.21,-20.34],[16.65,-20.72],[16.08,-21.08],
    [15.49,-21.41],[14.89,-21.7],[14.27,-21.97],[13.64,-22.21],[12.99,-22.42],
    [12.34,-22.6],[11.68,-22.74],[11.02,-22.85],[10.35,-22.94],[9.68,-22.98],
    [9,-23],[-9,-23],[-9.68,-22.98],[-10.35,-22.94],[-11.02,-22.85],
    [-11.68,-22.74],[-12.34,-22.6],[-12.99,-22.42],[-13.64,-22.21],[-14.27,-21.97],
    [-14.89,-21.7],[-15.49,-21.41],[-16.08,-21.08],[-16.65,-20.72],[-17.21,-20.34],
    [-17.75,-19.93],[-18.26,-19.5],[-18.76,-19.04],[-19.23,-18.56],[-19.68,-18.05],
    [-20.1,-17.53],[-20.5,-16.98],[-20.87,-16.42],[-21.22,-15.84],[-21.53,-15.24],
    [-21.8,-14.68],[-22.12,-13.88],[-22.33,-13.29],[-22.5,-12.7],[-22.65,-12.09],
    [-22.78,-11.48],[-22.88,-10.87],[-22.94,-10.25],[-23,-9],[-23.53,0.54],
    [-23.61,1.23],[-23.77,1.91],[-24,2.56],[-24.31,3.19],[-24.69,3.77],
    [-25.13,4.3],[-31.11,10.71],[-31.5,11.31],[-31.65,12.01],[-31.54,12.71],
    [-31.19,13.34],[-30.65,13.8],[-22.15,18.71],[-21.56,19.22],[-21.22,19.92],
    [-21.17,20.7],[-21.42,21.44],[-49.71,70.45],[-49.97,71.19],[-49.91,71.97],
    [-49.57,72.67],[-48.98,73.18],[-45.09,75.43],[-44.35,75.68],[-43.57,75.63],
    [-42.87,75.29],[-42.35,74.7],[-34.24,60.65],[-33.89,60.15],[-33.5,59.68],
    [-33.06,59.25],[-32.57,58.88],[-32.06,58.55],[-31.51,58.28],[-30.93,58.06],
    [-30.34,57.91],[-29.74,57.82],[-29.12,57.79],[29.12,57.79],[29.74,57.82],
    [30.34,57.91],[30.93,58.06],[31.51,58.28],[32.06,58.55],[32.57,58.88],
    [33.06,59.25],[33.5,59.68],[33.89,60.15],[34.24,60.65]]);
}
module Vertex_UpperFrameCut()
{
    linear_extrude(height = height+2, center = false, convexity = 10)polygon(points = 
    [[26.52,47.29],[26.76,47.94],[26.76,48.63],[26.52,49.29],[26.08,49.82],
    [25.48,50.16],[24.79,50.29],[-24.79,50.29],[-25.48,50.16],[-26.08,49.82],
    [-26.52,49.29],[-26.76,48.63],[-26.76,47.94],[-26.52,47.29],[-14.11,25.79],
    [-13.81,25.36],[-13.44,24.99],[-13.01,24.69],[-12.54,24.47],[-12.03,24.33],
    [-11.51,24.29],[11.51,24.29],[12.03,24.33],[12.54,24.47],[13.01,24.69],
    [13.44,24.99],[13.81,25.36],[14.11,25.79]]);
}
module VertexTop_EMT12_FullCut()
{
    translate([0,0,0])
    EMT12_4xCut();
}
module VertexTop_EMT12_HalfCut()
{
    difference()
    {
        EMT12_4xCut();
        if (Bot_EMT_Holes_ON == 1)
        {
            translate([-19.4,-5-30,-1])
            cube([38.8,10+30,height+4]);
        } else
        {
            translate([-19.4,-5,-1])
            cube([38.8,10,height+4]);
        }
        translate([0,0,-1])
        cylinder(d=14.5,h=height+4,$fn=68);     //Allow for extra space around center hole
        //%EMT12_Pipes();
    }
}
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

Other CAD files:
V2_EMT34_Horizontal_EMT12_Vertical/EMT34_V2_SideHoldingBracket_rev10.dxf
EMT34_Horizontal_2060_Vertical/EMT_Name_Rev2.stl
EMT34_Horizontal_EMT12_Vertical/VertexBot_2xEMTSH_4xEMTV_rev54_repaired.stl
FilamentHolder/SpoolHolder_EMT_2x_18mm_Base_Rev15.stl
EMT12_Horizontal_EMT12_Vertical/Delta_EMT_MicroMech_LimitSwitch2PartBracket_Rev17.scad
EMT12_Horizontal_EMT12_Vertical/BottomFrame/BottomDoveTailFrame_210mmOD_Parts_Rev30.stl
EMT12_Horizontal_EMT12_Vertical/BottomFrame/BottomDoveTailFrame_Rev30.scad
EMT12_Horizontal_EMT12_Vertical/BottomFrame/HB_EMT12_Bracket_Simple_rev2.stl
EMT12_Horizontal_EMT12_Vertical/BottomFrame/Vertex_2x_EM12TH_4xEMT12V_rev100.stl
EMT12_Horizontal_EMT12_Vertical/Delta_EMT_Mech_LimitSwitch2PartBracket_Rev17.stl
EMT12_Horizontal_EMT12_Vertical/Delta_EMT_MicroMech_LimitSwitch2PartBracket_Rev17.stl
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

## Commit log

2016-10-31 Add files via upload
    Added Brackets
    [EMT_BotSideHoldingBracket_1x_rev6.stl, EMT_BotSideHoldingBracket_rev6.scad, EMT_Emmett_NameBracket_rev3.scad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]
2016-10-31 Add files via upload
    Add Parts for using 1/2" EMT for the Verticals
    [Delta_EMT_Mech_LimitSwitch2PartBracket_Rev16.scad, Delta_EMT_Mech_LimitSwitch2PartBracket_Rev16.stl, Delta_EMT_MicroMech_LimitSwitch2PartBracket_Rev16.scad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]
2016-11-03 P/S Brackets for 1/2"EMT, 3/4"EMT or 1/2" PVC
    The DXF file has the profiles and cutouts that the openscad file uses to make either 1/2"EMT, 3/4"EMT or 1/2"PVC Power Supply holding bracket
    [EMT12_PS_Bracket_Rev4.stl, EMT34_PS_Bracket_Rev4.stl, PVC12_PS_Bracket_Rev4.stl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]
2016-11-03 Added Extended P/S Bracket
    This should allow for smaller build Diameters like 200mm
    [EMT12_PS_Bracket_Extend_Rev6.stl, EMT34_PS_Bracket_Extend_Rev6.stl, PVC12_PS_Bracket_Extend_Rev6.stl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]
2016-11-04 Updated Extended Brackets
    [EMT12_PS_Bracket_Extend_Rev7.stl, EMT34_PS_Bracket_Extend_Rev7.stl, PVC12_PS_Bracket_Extend_Rev7.stl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]
2016-11-04 Add files via upload
    Added Drilling Jigs oriented along X-Axis for Printing
    [HorizontalPipeDrill_Jig_12EMT_Rev3.stl, HorizontalPipeDrill_Jig_12PVC_Rev3.stl, HorizontalPipeDrill_Jig_34EMT_Rev3.stl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]
2016-11-06 Animation of Emmett
    This is an animation of an Emmett design using 1/2" EMT both horizontal & Vertical and sized for 210mm build plate & 800mm verticals.
2016-11-07 Animation of 266mm Horizontals & 800mm Verticals
    This configuration uses a 210mm Build Plate with 266mm Horizontal 1/2"EMT & 800mm Vertical 1/2"EMT
2016-11-07 420mm Horizontal 3/4"EMT & 1220mm Vertical 1/2" EMT
    This configuration uses a 280mm Build Plate with 420mm Horizontal 3/4"EMT & 1220mm Vertical 1/2"EMT
2016-11-07 Animation of Emmett-Delta
    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
2016-11-07 Animation of Emmett-Delta
    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
2016-11-07 Vertex for 1/2" EMT
    This vertex is for 1/2" EMT both Horizontal & Vertical
    [Vertex_2x_EM12TH_4xEMT12V_rev93.scad, Vertex_2x_EM12TH_4xEMT12V_rev93.stl]
2016-11-07 Add files via upload
    Added some print data comments to the file
    [HorizontalPipeDrill_Jig_Rev3.scad]
2016-11-07 Animation of Emmett-Delta
    This configuration uses a 210mm Build Plate with 260mm Horizontal 1/2"PVC & 800mm Vertical 1/2"EMT
2016-11-09 Frame Lengths Calculator For Different Configs
    This Excel spreadsheet will help you determine the lengths of EMT and/or PVC you need for different size builds.
    Enter your Heat Bed Diameter in Cell B2 & Vertical Length in I2
    The spreadsheet will fill in the Horizontal lengths & total lengths of pipe needed
    [Emmett-Delta_FrameLengths_Calculator.xls]
2016-11-10 Cobalt Griffonary's BOM list
    [BasicBillOfMatterials_EMT34H_EMT12V.xls]
2016-11-21 Updated Vertex Parts
    Made some minor corrections & added Vertex specific to top idler connection. Vertex_2x_EMT12H_4xEMT12V.stl can be used for either bottom or top if you do not want the idler adjustment. VertexTop_2x_EMT12_4xEMT12V_rev96.stl uses a little less plastic than vertex that can be used for both bottom or top.
    [VertexTop_2x_EMT12H_4xEMT12V_rev96.scad, VertexTop_2x_EMT12H_4xEMT12V_rev96.stl, Vertex_2x_EMT12H_4xEMT12V_rev96.scad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]
2016-11-21 Updated Idler Plate & Vertex Parts
    Uploaded only the STL file for this until I fine tune the assembly portion of the openscad file
    [Idler_2holeMount_38mmHoleSpacing_rev19.stl]
2016-11-28 Minor changes to Vertex Parts
    Made the end slot opening 1mm wider & open to the bottom as well as changing the diameter cuts of the vertical 1/2" EMT from18.4mm to 18.2mm OD. This is a better fit for me.
    [VertexTop_2x_EM12TH_4xEMT12V_rev100.scad, VertexTop_2x_EM12TH_4xEMT12V_rev100.stl, Vertex_2x_EM12TH_4xEMT12V_rev100.scad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]
2016-11-28 Optional Frame A
    [BottomDoveTailFrame_210mmOD_Parts_Rev28.stl, BottomDoveTailFrame_300mmOD_Parts_Rev28.stl, BottomDoveTailFrame_Rev28.scad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]
2016-11-28 DoveTail Frame Internal Assembly
    [BottomDoveTailFrame_210mmOD_Parts_Rev28.stl, BottomDoveTailFrame_300mmOD_Parts_Rev28.stl, BottomDoveTailFrame_Rev28.scad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]
2016-11-29 Vertex Brackets
    Brackets to hold the 1/2" EMT Horizontal pipe to the Vertex and/or Inner Dovetail Frame.
    [EMT_18mmVertexBrackets_Rev2.scad, EMT_18mmVertex_DoveTailBrackets_Rev2.stl, EMT_18mmVertex_SimpleBrackets_Rev2.stl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]
2016-11-29 Cleaned up the code
    Only cleaned up the code, the STL parts did not change
    [EMT_18mmVertexBrackets_Rev3.scad]
2016-11-29 Fixed Interference Problem with HB Bracket
    After looking at the Assembly with the Heat Bed Bracket, I noticed an interference problem. I changed the parts that would hit that & also added the 2 .stl files that the openscad file references.
    [BottomDoveTailFrame_210mmOD_Parts_Rev30.stl, BottomDoveTailFrame_300mmOD_Parts_Rev30.stl, BottomDoveTailFrame_Rev30.scad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]
2016-11-30 Version 2 of 3/4" Horizontal EMT Vertex
    [VertexTop_2x_EM34TH_4xEMT12V_V2_rev101.scad, VertexTop_2x_EM34TH_4xEMT12V_V2_rev101.stl, Vertex_2x_EMT34H_4xEMT12V_V2_rev101.scad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]
2016-11-30 Added new version of Heat Bed Bracket
    I added the Version 2 of the 3/4" EMT Heat Bed Bracket
    [HB_EMT12_Bracket_rev3.stl, HB_EMT34_Bracket_rev3.stl, HB_EMT34_V2_Bracket_rev3.stl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]
2016-11-30 V2 Brackets
    [EMT34_V2_SideHoldingBracket_rev10.dxf, EMT34_V2_SideHoldingBracket_rev11.scad, EMT34_V2_SideHoldingBrackets_rev11.stl]
